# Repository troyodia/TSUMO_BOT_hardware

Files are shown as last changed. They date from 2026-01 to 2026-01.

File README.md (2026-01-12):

# TSUMO_BOT_hardware

This repository contains the schematic and PCB designs for TSUMO_BOT a sumo robot (12x12cm), created in KiCad and manufactured by JLCPCB. The PCB is a 4-layer board, with an STM32L476RG microcontroller, two motor drivers TB6612FNG, an IR reciever TSP382, MOSFET circuit protection FDS6687, a 5V buck converter RT8259, a 3.3V regulator AMS1117, a 5V power mux TPS2116DRL and a USB-C connector with ESD protection (USBLC6).

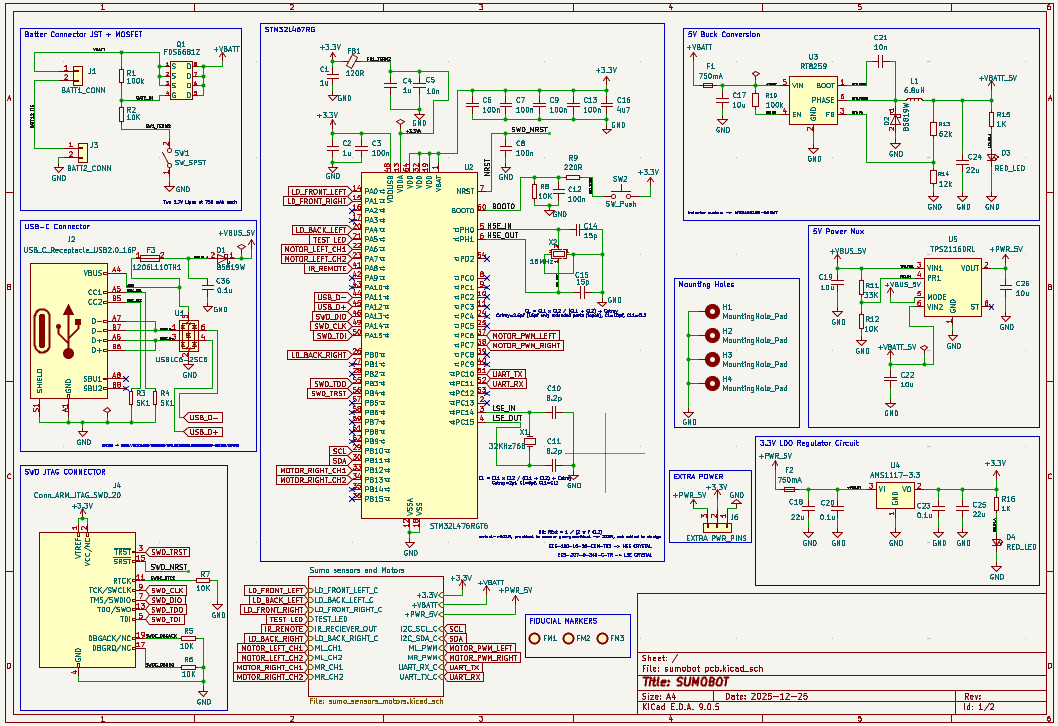
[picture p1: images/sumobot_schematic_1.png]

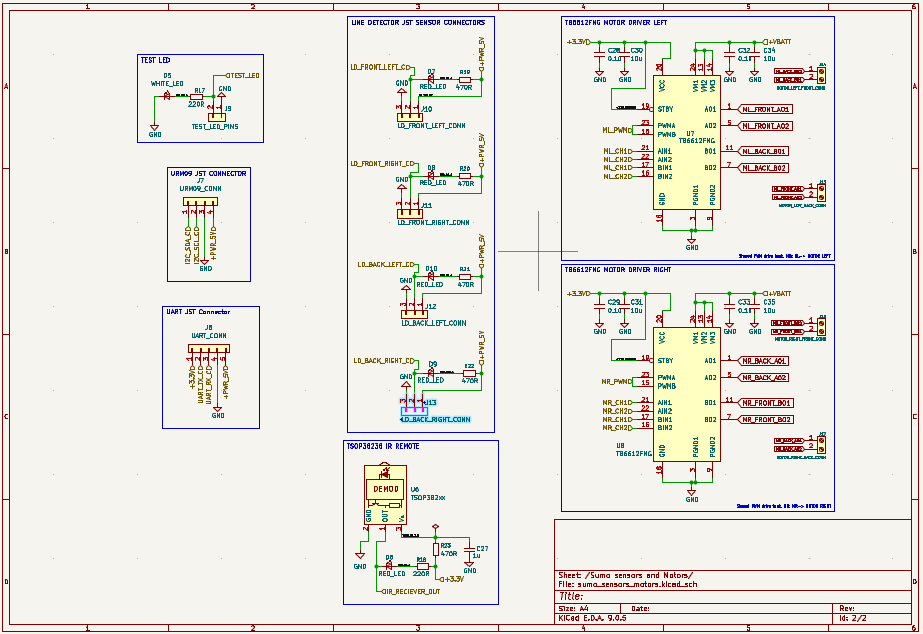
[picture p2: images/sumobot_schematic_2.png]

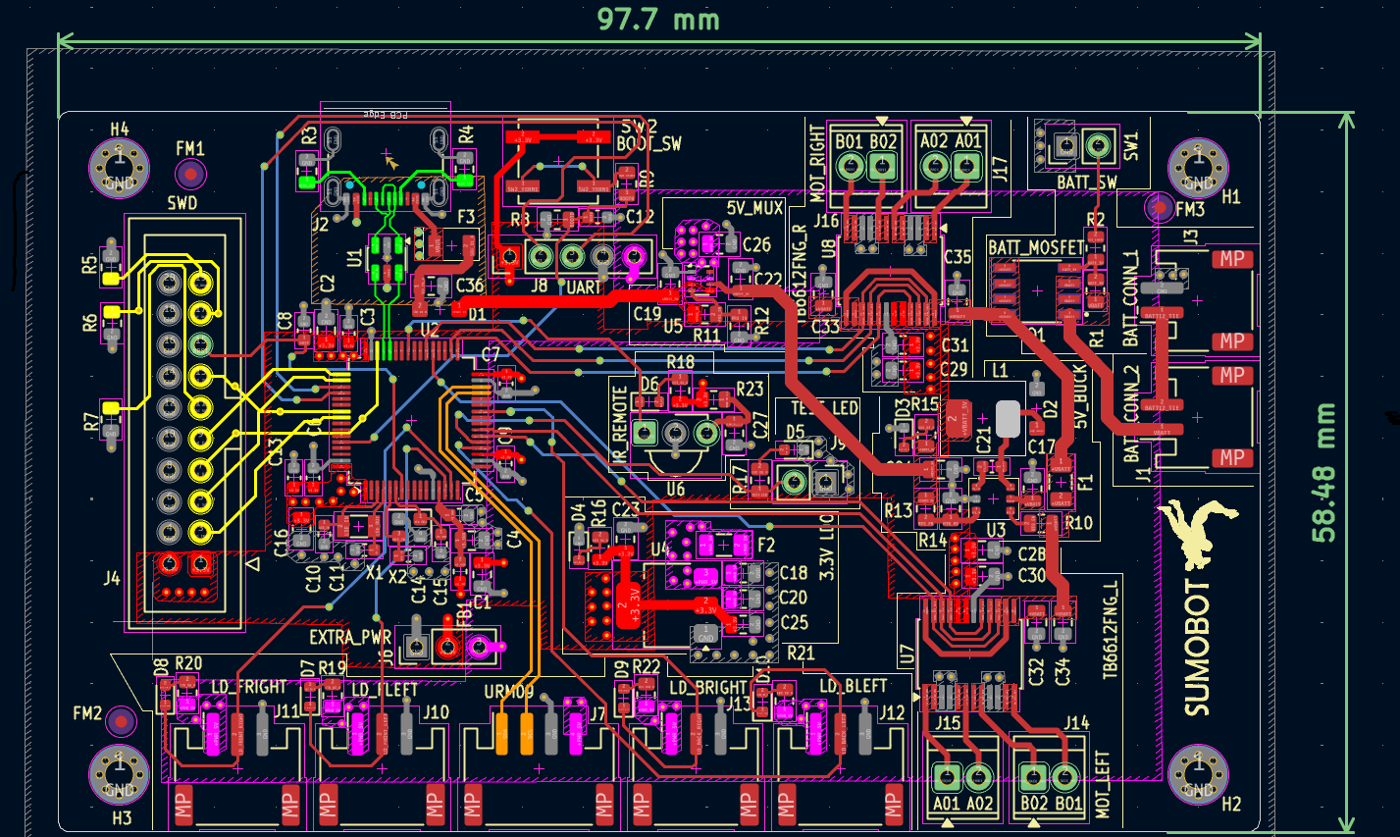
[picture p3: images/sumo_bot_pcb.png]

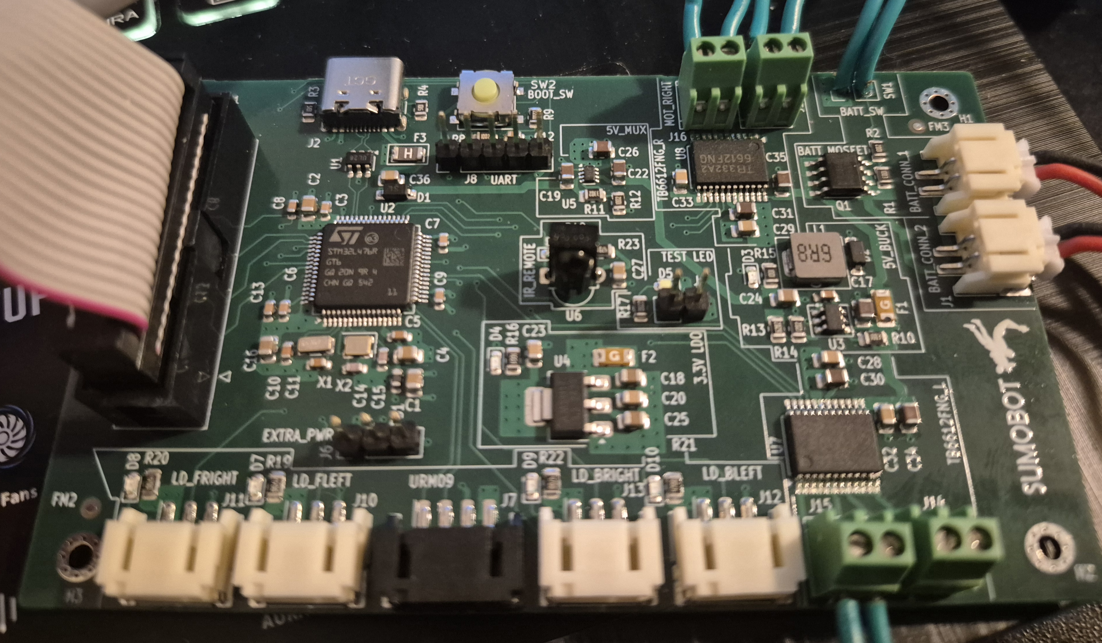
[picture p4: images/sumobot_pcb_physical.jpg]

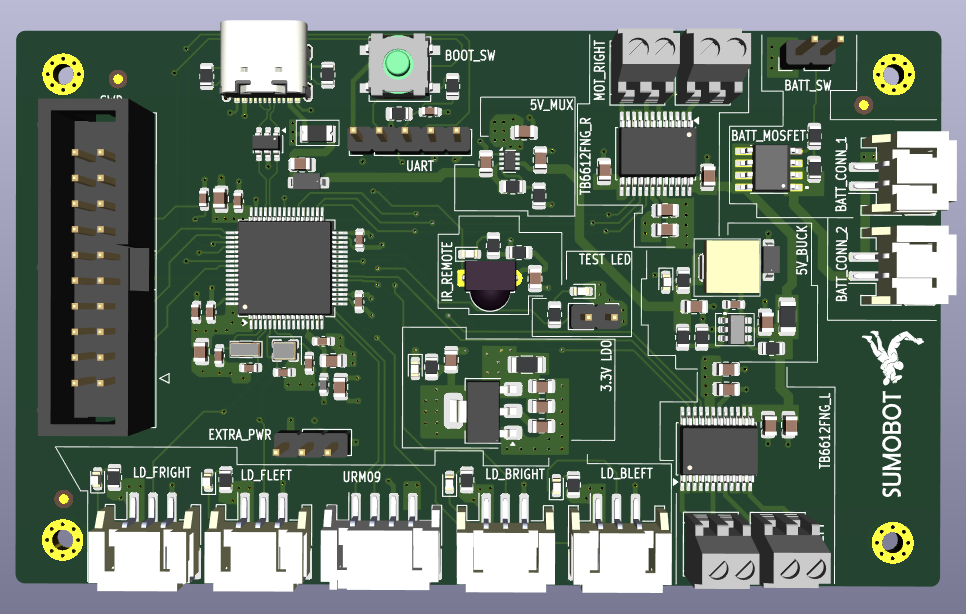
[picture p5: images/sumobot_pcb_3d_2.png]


## Setup

First clone the repo:

```
git clone https://github.com/troyodia/TSUMO_BOT_hardware.git
```

Import the project into KiCad 9.0 and make sure you have the "default global symbol library table" and the "default footprint library" available. KiCad should find the 3Dmodels and symbols under libs/ automatically. You must manually import the footprints under libs/footprints/ (select "file/add library" from the menu in the footprint editor and add them to the project).

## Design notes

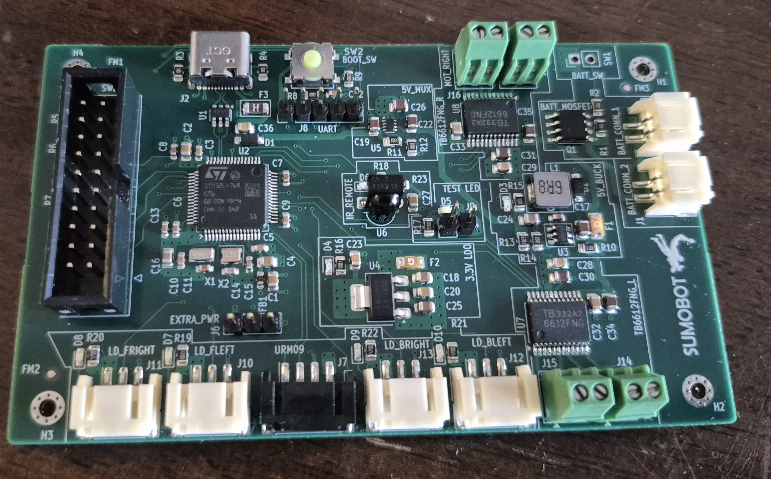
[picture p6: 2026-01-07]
PCB physical.jpg

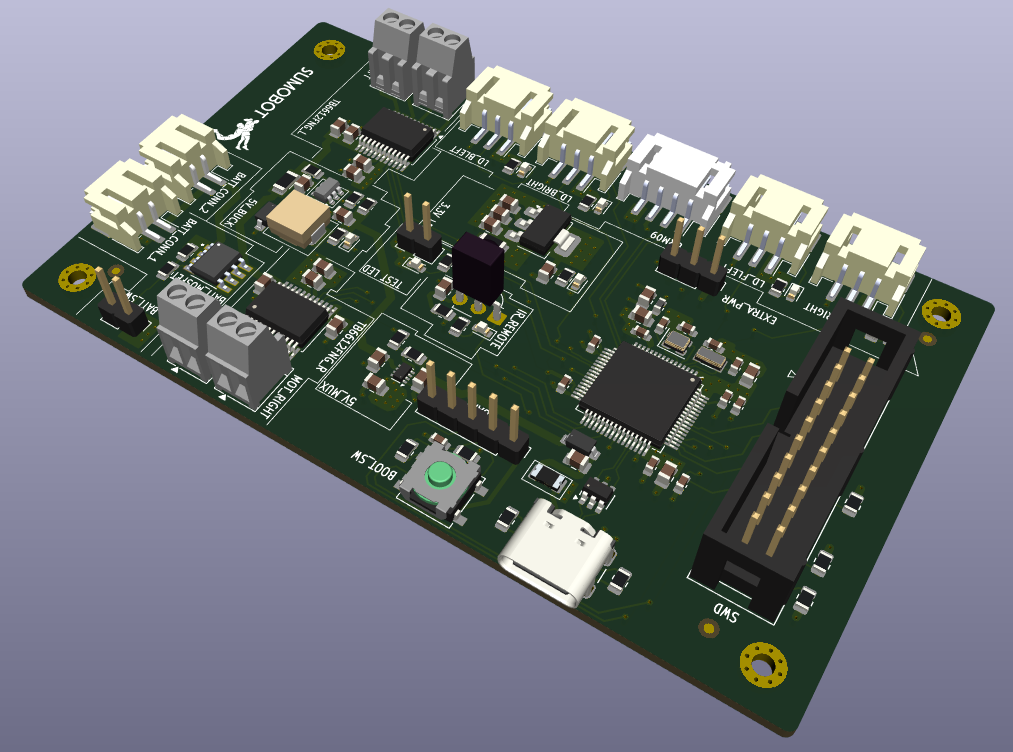
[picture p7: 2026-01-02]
images/sumobot_pcb_3d_1.png

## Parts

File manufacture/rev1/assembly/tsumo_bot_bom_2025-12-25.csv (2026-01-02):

Reference | Qty | Value | Exclude from BOM | Footprint | Datasheet | LCSC
X2 | 1 | 16MHz |  | Crystal:Crystal_SMD_2520-4Pin_2.5x2.0mm | ~ | C7270509
X1 | 1 | 32KHz768 |  | Crystal:Crystal_SMD_3215-2Pin_3.2x1.5mm | ~ | C5633029
U5 | 1 | TPS2116DRL |  | Package_TO_SOT_SMD:SOT-583-8 | https://www.ti.com/lit/ds/symlink/tps2116.pdf | C3235557
J2 | 1 | USB_C_Receptacle_USB2.0_16P |  | Connector_USB:USB_C_Receptacle_GCT_USB4105-xx-A_16P_TopMnt_Horizontal | https://www.usb.org/sites/default/files/documents/usb_type-c.zip | C3020560
C10,C11 | 2 | 8.2p |  | Capacitor_SMD:C_0603_1608Metric | ~ | C1322360
C17,C19,C22,C26,C30,C31,C34,C35 | 8 | 10u |  | Capacitor_SMD:C_0805_2012Metric | ~ | C440198
L1 | 1 | 6.8uH |  | MWSA0518S-6R8MT:MWSA0518S-6R8MT | https://mm.digikey.com/Volume0/opasdata/d220001/medias/docus/2905/MWSA-S_Series_DS.pdf | C408348
SW2 | 1 | SW_Push |  | Button_Switch_SMD:SW_SPST_B3SL-1002P | ~ | C306880
J3 | 1 | BATT2_CONN |  | Connector_JST:JST_PH_S2B-PH-SM4-TB_1x02-1MP_P2.00mm_Horizontal | ~ | C295747
J1 | 1 | BATT1_CONN |  | Connector_JST:JST_PH_S2B-PH-SM4-TB_1x02-1MP_P2.00mm_Horizontal | ~ | C295747
J7 | 1 | URM09_CONN |  | Connector_JST:JST_PH_S4B-PH-SM4-TB_1x04-1MP_P2.00mm_Horizontal | ~ | C265332
J13 | 1 | LD_BACK_RIGHT_CONN |  | Connector_JST:JST_PH_S3B-PH-SM4-TB_1x03-1MP_P2.00mm_Horizontal | ~ | C265101
J12 | 1 | LD_BACK_LEFT_CONN |  | Connector_JST:JST_PH_S3B-PH-SM4-TB_1x03-1MP_P2.00mm_Horizontal | ~ | C265101
J11 | 1 | LD_FRONT_RIGHT_CONN |  | Connector_JST:JST_PH_S3B-PH-SM4-TB_1x03-1MP_P2.00mm_Horizontal | ~ | C265101
J10 | 1 | LD_FRONT_LEFT_CONN |  | Connector_JST:JST_PH_S3B-PH-SM4-TB_1x03-1MP_P2.00mm_Horizontal | ~ | C265101
Q1 | 1 | FDS6681Z |  | FDS6681Z:FDS6681Z_Footprint | https://jlcpcb.com/api/file/downloadByFileSystemAccessId/8589837231214133248 | C236906
F1,F2 | 2 | 750mA |  | Fuse:Fuse_1206_3216Metric | ~ | C187594
R13 | 1 | 62k |  | Resistor_SMD:R_0805_2012Metric | ~ | C178156
R1,R10 | 2 | 100k |  | Resistor_SMD:R_0805_2012Metric | ~ | C149504
U7,U8 | 2 | TB6612FNG |  | Package_SO:SSOP-24_5.3x8.2mm_P0.65mm | https://toshiba.semicon-storage.com/us/product/linear/motordriver/detail.TB6612FNG.html | C141517
F3 | 1 | 1206L110TH1 |  | 1206L110TH1_SMT:1206L110THYR_SMT | https://jlcpcb.com/api/file/downloadByFileSystemAccessId/8588884694661914624 | C126818
U2 | 1 | STM32L476RGT6 |  | Package_QFP:LQFP-64_10x10mm_P0.5mm | https://www.st.com/resource/en/datasheet/stm32l476rg.pdf | C74797
C5,C21 | 2 | 10n |  | Capacitor_SMD:C_0603_1608Metric | ~ | C57112
C18,C24,C25 | 3 | 22u |  | Capacitor_SMD:C_0805_2012Metric | ~ | C45783
C1,C2,C4,C27 | 4 | 1u |  | Capacitor_SMD:C_0805_2012Metric | ~ | C28323
R3,R4 | 2 | 5K1 |  | Resistor_SMD:R_0805_2012Metric |  | C27834
R19,R20,R21,R22,R23 | 5 | 470R |  | Resistor_SMD:R_0805_2012Metric | ~ | C17710
R11 | 1 | 33K |  | Resistor_SMD:R_0805_2012Metric |  | C17633
R9,R17,R18 | 3 | 220R |  | Resistor_SMD:R_0805_2012Metric | ~ | C17557
R15,R16 | 2 | 1K |  | Resistor_SMD:R_0805_2012Metric |  | C17513
R14 | 1 | 12k |  | Resistor_SMD:R_0805_2012Metric | ~ | C17444
R2,R5,R6,R7,R8,R12 | 6 | 10K |  | Resistor_SMD:R_0805_2012Metric |  | C17414
U3 | 1 | RT8259 |  | RT8259GE:RT8259GE_RT8259GE SOT-23-6 Surface Mount | https://www.richtek.com/SaveDownload.aspx?specid=RT8259 | C16819
FB1 | 1 | 120R |  | Inductor_SMD:L_0603_1608Metric | ~ | C14709
C3,C6,C7,C8,C9,C12,C13 | 7 | 100n |  | Capacitor_SMD:C_0603_1608Metric | ~ | C14663
D1,D2 | 2 | B5819W |  | Schottky Diode Custom:B5819W SOD123 | https://jlcpcb.com/api/file/downloadByFileSystemAccessId/8586175589875396608 | C8598
U1 | 1 | USBLC6-2SC6 |  | Package_TO_SOT_SMD:SOT-23-6 | https://www.st.com/resource/en/datasheet/usblc6-2.pdf | C7519
U4 | 1 | AMS1117-3.3 |  | Package_TO_SOT_SMD:SOT-223-3_TabPin2 | http://www.advanced-monolithic.com/pdf/ds1117.pdf | C6186
D5 | 1 | WHITE_LED |  | LED_SMD:LED_0603_1608Metric | ~ | C2290
D3,D4,D6,D7,D8,D9,D10 | 7 | RED_LED |  | LED_SMD:LED_0603_1608Metric | ~ | C2286
C16 | 1 | 4u7 |  | Capacitor_SMD:C_0805_2012Metric | ~ | C1779
C20,C23,C28,C29,C32,C33,C36 | 7 | 0.1u |  | Capacitor_SMD:C_0805_2012Metric | ~ | C1711
C14,C15 | 2 | 15p |  | Capacitor_SMD:C_0603_1608Metric | ~ | C1644
U6 | 1 | TSOP382xx | Excluded from BOM | OptoDevice:Vishay_MINICAST-3Pin | http://www.vishay.com/docs/82491/tsop382.pdf
SW1 | 1 | SW_SPST | Excluded from BOM | Connector_PinHeader_2.54mm:PinHeader_1x02_P2.54mm_Vertical | ~
J17 | 1 | MOTOR_RIGHT_BACK_CONN | Excluded from BOM | TerminalBlock_TE-Connectivity:TerminalBlock_TE_282834-2_1x02_P2.54mm_Horizontal | ~
J16 | 1 | MOTOR_RIGHT_FRONT_CONN | Excluded from BOM | TerminalBlock_TE-Connectivity:TerminalBlock_TE_282834-2_1x02_P2.54mm_Horizontal | ~
J15 | 1 | MOTOR_LEFT_BACK_CONN | Excluded from BOM | TerminalBlock_TE-Connectivity:TerminalBlock_TE_282834-2_1x02_P2.54mm_Horizontal | ~
J14 | 1 | MOTOR_LEFT_FRONT_CONN | Excluded from BOM | TerminalBlock_TE-Connectivity:TerminalBlock_TE_282834-2_1x02_P2.54mm_Horizontal | ~
J9 | 1 | TEST_LED_PINS | Excluded from BOM | Connector_PinHeader_2.54mm:PinHeader_1x02_P2.54mm_Vertical | ~
J8 | 1 | UART_CONN | Excluded from BOM | Connector_PinHeader_2.54mm:PinHeader_1x05_P2.54mm_Vertical | ~
J6 | 1 | EXTRA PWR_PINS | Excluded from BOM | Connector_PinHeader_2.54mm:PinHeader_1x03_P2.54mm_Vertical | ~
J4 | 1 | Conn_ARM_JTAG_SWD_20 | Excluded from BOM | Connector_IDC:IDC-Header_2x10_P2.54mm_Vertical | http://infocenter.arm.com/help/topic/com.arm.doc.dui0499b/DUI0499B_system_design_reference.pdf
H1,H2,H3,H4 | 4 | MountingHole_Pad | Excluded from BOM | MountingHole:MountingHole_2.2mm_M2_Pad_Via | ~
FM1,FM2,FM3 | 3 | Fiducial | Excluded from BOM | Fiducial:Fiducial_1mm_Mask2mm | ~

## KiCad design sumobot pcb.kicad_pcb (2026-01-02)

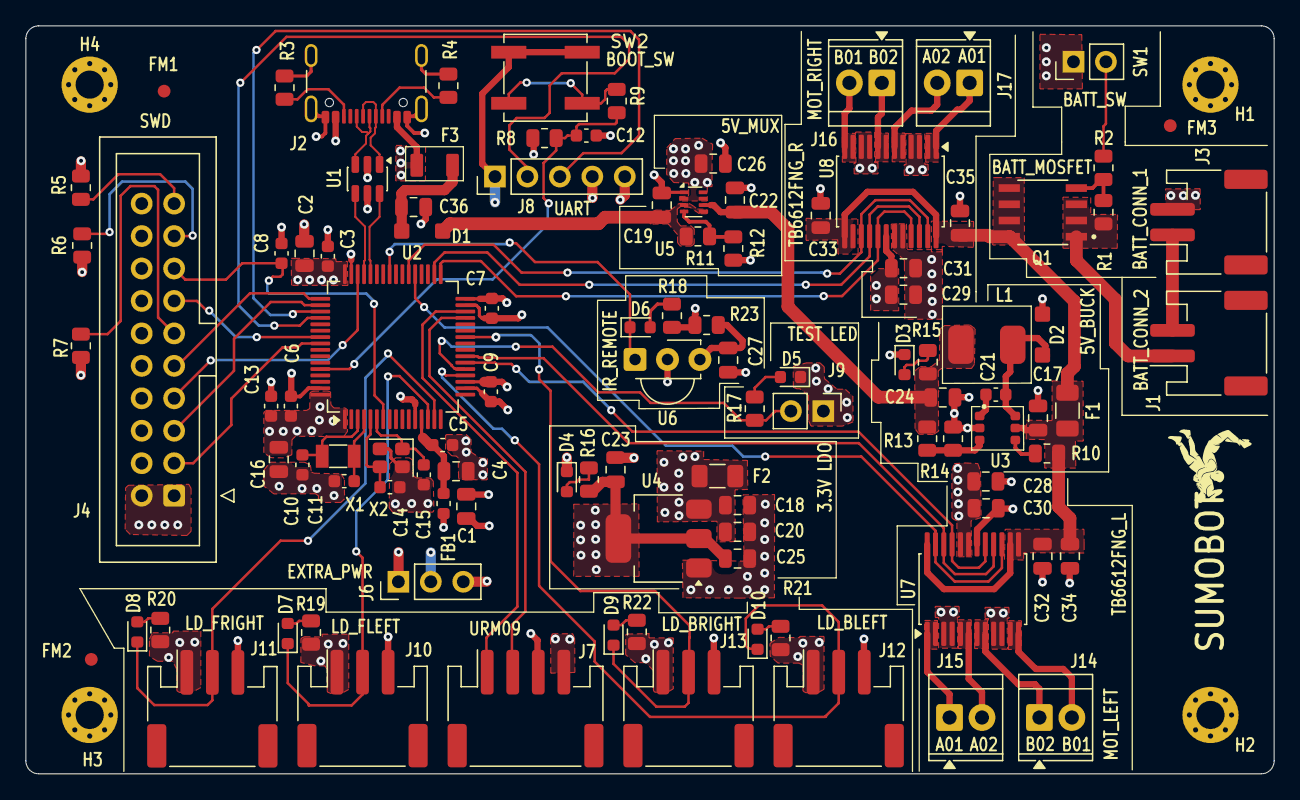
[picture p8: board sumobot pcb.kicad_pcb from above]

Board: 4 copper layers, 97.7 x 58.5 mm, 110 parts (0 on the bottom side), 72 nets.

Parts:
C1, C2, C4, C27: 1u; C_0805_2012Metric
C3, C6, C7, C8, C9, C12, C13: 100n; C_0603_1608Metric
C5, C21: 10n; C_0603_1608Metric
C10, C11: 8.2p; C_0603_1608Metric
C14, C15: 15p; C_0603_1608Metric
C16: 4u7; C_0805_2012Metric
C17, C19, C22, C26, C30, C31, C34, C35: 10u; C_0805_2012Metric
C18, C24, C25: 22u; C_0805_2012Metric
C20, C23, C28, C29, C32, C33, C36: 0.1u; C_0805_2012Metric
D1, D2: B5819W; B5819W SOD123
D3, D4, D6, D7, D8, D9, D10: RED_LED; LED_0603_1608Metric
D5: WHITE_LED; LED_0603_1608Metric
F1, F2: 750mA; Fuse_1206_3216Metric
F3: 1206L110TH1; 1206L110THYR_SMT
FB1: 120R; L_0603_1608Metric
FM1, FM2, FM3: Fiducial; Fiducial_1mm_Mask2mm
H1, H2, H3, H4: MountingHole_Pad; MountingHole_2.2mm_M2_Pad_Via
J1: BATT1_CONN; JST_PH_S2B-PH-SM4-TB_1x02-1MP_P2.00mm_Horizontal
J2: USB_C_Receptacle_USB2.0_16P; USB_C_Receptacle_GCT_USB4105-xx-A_16P_TopMnt_Horizontal
J3: BATT2_CONN; JST_PH_S2B-PH-SM4-TB_1x02-1MP_P2.00mm_Horizontal
J4: Conn_ARM_JTAG_SWD_20; IDC-Header_2x10_P2.54mm_Vertical
J6: EXTRA PWR_PINS; PinHeader_1x03_P2.54mm_Vertical
J7: URM09_CONN; JST_PH_S4B-PH-SM4-TB_1x04-1MP_P2.00mm_Horizontal
J8: UART_CONN; PinHeader_1x05_P2.54mm_Vertical
J9: TEST_LED_PINS; PinHeader_1x02_P2.54mm_Vertical
J10: LD_FRONT_LEFT_CONN; JST_PH_S3B-PH-SM4-TB_1x03-1MP_P2.00mm_Horizontal
J11: LD_FRONT_RIGHT_CONN; JST_PH_S3B-PH-SM4-TB_1x03-1MP_P2.00mm_Horizontal
J12: LD_BACK_LEFT_CONN; JST_PH_S3B-PH-SM4-TB_1x03-1MP_P2.00mm_Horizontal
J13: LD_BACK_RIGHT_CONN; JST_PH_S3B-PH-SM4-TB_1x03-1MP_P2.00mm_Horizontal
J14: MOTOR_LEFT_FRONT_CONN; TerminalBlock_TE_282834-2_1x02_P2.54mm_Horizontal
J15: MOTOR_LEFT_BACK_CONN; TerminalBlock_TE_282834-2_1x02_P2.54mm_Horizontal
J16: MOTOR_RIGHT_FRONT_CONN; TerminalBlock_TE_282834-2_1x02_P2.54mm_Horizontal
J17: MOTOR_RIGHT_BACK_CONN; TerminalBlock_TE_282834-2_1x02_P2.54mm_Horizontal
L1: 6.8uH; MWSA0518S-6R8MT
Q1: FDS6681Z; FDS6681Z_Footprint
R1, R10: 100k; R_0805_2012Metric
R2, R5, R6, R7, R8, R12: 10K; R_0805_2012Metric
R3, R4: 5K1; R_0805_2012Metric
R9, R17, R18: 220R; R_0805_2012Metric
R11: 33K; R_0805_2012Metric
R13: 62k; R_0805_2012Metric
R14: 12k; R_0805_2012Metric
R15, R16: 1K; R_0805_2012Metric
R19, R20, R21, R22, R23: 470R; R_0805_2012Metric
SW1: SW_SPST; PinHeader_1x02_P2.54mm_Vertical
SW2: SW_Push; SW_SPST_B3SL-1002P
U1: USBLC6-2SC6; SOT-23-6
U2: STM32L476RGT6; LQFP-64_10x10mm_P0.5mm
U3: RT8259; RT8259GE_RT8259GE SOT-23-6 Surface Mount
U4: AMS1117-3.3; SOT-223-3_TabPin2
U5: TPS2116DRL; SOT-583-8
U6: TSOP382xx; Vishay_MINICAST-3Pin
U7, U8: TB6612FNG; SSOP-24_5.3x8.2mm_P0.65mm
X1: 32KHz768; Crystal_SMD_3215-2Pin_3.2x1.5mm
X2: 16MHz; Crystal_SMD_2520-4Pin_2.5x2.0mm

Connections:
+3.3V: C1.1, C2.1, C3.1, C6.1, C7.1, C9.1, C13.1, C16.1, C23.1, C25.1, C28.1, C29.1, C30.1, C31.1, FB1.1, J4.1 (VTREF), J4.2 (VCC/NC), J6.2, J8.1, R16.1, R18.2, R23.2, SW2.2, U2.1 (VBAT), U2.19 (VDD), U2.32 (VDD), U2.48 (VDDUSB), U2.64 (VDD), U4.2 (VO), U7.19 (STBY), U7.20 (VCC), U8.19 (STBY), U8.20 (VCC)
+PWR_5V: C18.1, C20.1, C26.1, F2.1, F2.2, J6.3, J7.4, J8.5, J10.1, J11.1, J12.1, J13.1, R19.1, R20.1, R21.1, R22.1, U4.3 (VI), U5.2 (VOUT), U5.7 (VOUT)
+VBATT: C17.1, C32.1, C33.1, C34.1, C35.1, F1.1, F1.2, Q1.5 (D), Q1.6 (D), Q1.7 (D), Q1.8 (D), R10.1, U3.5 (VIN), U7.13 (VM2), U7.14 (VM3), U7.24 (VM1), U8.13 (VM2), U8.14 (VM3), U8.24 (VM1)
+VBATT_5V: C22.1, C24.1, L1.2, R13.1, R15.1, U5.6 (VIN2)
+VBUS_5V: C19.1, D1.1 (K), R11.1, U5.3 (VIN1), U5.5 (MODE)
/+3.3VA: C4.1, C5.1, FB1.2, U2.13 (VDDA)
/BATT12_TIE: J1.2, J3.1
/BOOT0: C12.1, R8.1, R9.1, U2.60 (BOOT0)
/GATE_IN: Q1.4 (G), R1.2, R2.1
/HSE_IN: C14.1, U2.5 (PH0), X2.3
/HSE_OUT: C15.1, U2.6 (PH1), X2.1
/LED_D3_A: D3.2 (A), R15.2
/LED_D4_A: D4.2 (A), R16.2
/LSE_IN: C10.1, U2.3 (PC14), X1.2
/LSE_OUT: C11.1, U2.4 (PC15), X1.1
/NRST: C8.1, J4.15 (~SRST), U2.7 (NRST)
/PR1_IN: R11.2, R12.1, U5.4 (PR1)
/RT8_BOOT: C21.2, U3.1 (BOOT)
/RT8_EN: R10.2, U3.4 (EN)
/RT8_FB: R13.2, R14.1, U3.3 (FB)
/RT8_PHASE: C21.1, D2.1 (K), L1.1, U3.6 (PHASE)
/SCH_D1_A: C36.1, D1.2 (A), F3.2
/SW1_TERM2: R2.2, SW1.2 (B)
/SW2_TERM1: R9.2, SW2.1
/SWDC_DBGACK: J4.19 (DBGACK/NC), R5.1
/SWDC_DBGRQ: J4.17 (DBGRQ/NC), R6.1
/SWDC_RTCK: J4.11 (RTCK), R7.1
/Sumo sensors and Motors/LED_D5_A: D5.2 (A), R17.2
/Sumo sensors and Motors/LED_D6_A: D6.2 (A), R18.1
/Sumo sensors and Motors/LED_D7_A: D7.2 (A), R19.2
/Sumo sensors and Motors/LED_D8_A: D8.2 (A), R20.2
/Sumo sensors and Motors/LED_D9_A: D10.2 (A), R21.2
/Sumo sensors and Motors/LED_D10_A: D9.2 (A), R22.2
/Sumo sensors and Motors/TSOP_VS_3.3: C27.1, R23.1, U6.3 (Vs)
/USBC_CC1: J2.A5 (CC1), R4.1
/USBC_CC2: J2.B5 (CC2), R3.1
/USBC_D+: J2.A6 (D+), J2.B6 (D+), U1.3 (I/O2)
/USBC_D-: J2.A7 (D-), J2.B7 (D-), U1.1 (I/O1)
/VBATT: J1.1, Q1.1 (S), Q1.2 (S), Q1.3 (S), R1.1
/VBUS: F3.1, J2.A4 (VBUS), J2.A9 (VBUS), J2.B4 (VBUS), J2.B9 (VBUS), U1.5 (VBUS)
GND: C1.2, C2.2, C3.2, C4.2, C5.2, C6.2, C7.2, C8.2, C9.2, C10.2, C11.2, C12.2, C13.2, C14.2, C15.2, C16.2, C17.2, C18.2, C19.2, C20.2, C22.2, C23.2, C24.2, C25.2, C26.2, C27.2, C28.2, C29.2, C30.2, C31.2, C32.2, C33.2, C34.2, C35.2, C36.2, D2.2 (A), D3.1 (K), D4.1 (K), D5.1 (K), H1.1, H2.1, H3.1, H4.1, J2.A1 (GND), J2.A12 (GND), J2.B1 (GND), J2.B12 (GND), J2.S1 (SHIELD), J3.2, J4.4 (GND), J4.6 (GND), J4.8 (GND), J4.10 (GND), J4.12 (GND), J4.14 (GND), J4.16 (GND), J4.18 (GND), J4.20 (GND), J6.1, J7.3, J8.4, J9.1, J10.3, J11.3, J12.3, J13.3, R3.2, R4.2, R5.2, R6.2, R7.2, R8.2, R12.2, R14.2, SW1.1 (A), U1.2 (GND), U2.12 (VSSA), U2.18 (VSS), U2.31 (VSS), U2.47 (VSS), U2.63 (VSS), U3.2 (GND), U4.1 (GND), U5.1 (GND), U6.2 (GND), U7.3 (PGND1), U7.4 (PGND1), U7.9 (PGND2), U7.10 (PGND2), U7.18 (GND), U8.3 (PGND1), U8.4 (PGND1), U8.9 (PGND2), U8.10 (PGND2), U8.18 (GND), X2.2, X2.4
IR_REMOTE: D6.1 (K), U2.41 (PA8), U6.1 (OUT)
LD_BACK_LEFT: D10.1 (K), J12.2, U2.20 (PA4)
LD_BACK_RIGHT: D9.1 (K), J13.2, U2.26 (PB0)
LD_FRONT_LEFT: D7.1 (K), J10.2, U2.14 (PA0)
LD_FRONT_RIGHT: D8.1 (K), J11.2, U2.15 (PA1)
ML_BACK_B01: J14.2, U7.11 (BO1), U7.12 (BO1)
ML_BACK_B02: J14.1, U7.7 (BO2), U7.8 (BO2)
ML_FRONT_AO1: J15.1, U7.1 (AO1), U7.2 (AO1)
ML_FRONT_AO2: J15.2, U7.5 (AO2), U7.6 (AO2)
MOTOR_LEFT_CH1: U2.22 (PA6), U7.17 (BIN1), U7.21 (AIN1)
MOTOR_LEFT_CH2: U2.23 (PA7), U7.16 (BIN2), U7.22 (AIN2)
MOTOR_PWM_LEFT: U2.37 (PC6), U7.15 (PWMB), U7.23 (PWMA)
MOTOR_PWM_RIGHT: U2.38 (PC7), U8.15 (PWMB), U8.23 (PWMA)
MOTOR_RIGHT_CH1: U2.33 (PB12), U8.17 (BIN1), U8.21 (AIN1)
MOTOR_RIGHT_CH2: U2.34 (PB13), U8.16 (BIN2), U8.22 (AIN2)
MR_BACK_A01: J17.1, U8.1 (AO1), U8.2 (AO1)
MR_BACK_A02: J17.2, U8.5 (AO2), U8.6 (AO2)
MR_FRONT_BO1: J16.2, U8.11 (BO1), U8.12 (BO1)
MR_FRONT_BO2: J16.1, U8.7 (BO2), U8.8 (BO2)
SCL: J7.2, U2.29 (PB10)
SDA: J7.1, U2.30 (PB11)
SWD_CLK: J4.9 (TCK/SWCLK), U2.49 (PA14)
SWD_DIO: J4.7 (TMS/SWDIO), U2.46 (PA13)
SWD_TDI: J4.5 (TDI), U2.50 (PA15)
SWD_TDO: J4.13 (TDO/SWO), U2.55 (PB3)
SWD_TRST: J4.3 (~TRST), U2.56 (PB4)
TEST LED: J9.2, R17.1, U2.21 (PA5)
UART_RX: J8.2, U2.52 (PC11)
UART_TX: J8.3, U2.51 (PC10)
USB_D+: U1.4 (I/O2), U2.45 (PA12)
USB_D-: U1.6 (I/O1), U2.44 (PA11)

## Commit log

2026-01-02 uploaded manufacturing files for rev1 of pcb
    [sumobot pcb-B_Cu.gbl, sumobot pcb-B_Mask.gbs, sumobot pcb-B_Paste.gbp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]
2026-01-02 uploaded library files for rev1 of pcb
2026-01-02 uploaded images and created readme file
    [sumobot pcb.kicad_pcb, sumobot pcb.kicad_sch]
2026-01-07 added physical pcb image
2026-01-12 Updated PCB images
